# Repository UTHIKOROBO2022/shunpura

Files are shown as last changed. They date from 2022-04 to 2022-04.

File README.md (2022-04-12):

## はじめに  

2021年12月に開催された「第17回全日本学生飛行ロボットコンテスト」に東京大学の有志学生が集まって参加したチーム「瞬着とプライマーよこせ！」のメンバーが、出場機体に搭載した半自動操縦用の制御回路とソースコードを全て公開します！  

<br>

## ファイルリスト  

|ファイル名|説明|
|:--|:--|
|Neve.pdf|回路図PDF|
|Neve.sch|EAGLE回路図ファイル|
|Neve.brd|EAGLEボード図ファイル|
|control_Neve.ino|Arduinoソースファイル|
|CAD|機体の設計データ|

回路図ファイルとボード図ファイルは、Fusion360で作成したものをEAGLE形式で出力しています。

<br>

## 制御について  

本チームは自動操縦部門ではなく一般部門に出場しましたが、飛行を安定させ操縦しやすくするため、独自にマイコンや6軸ジャイロセンサを搭載して半自動操縦を実現しています。すなわち、手元の送信機の左スティックで姿勢角の目標値を与え、機体に搭載したマイコンでそれに追従するよう制御を行っています。また、S.BUS信号のCh.5に半自動操縦のON/OFF、Ch.6に投下機構の動作をアサインしています。

<br>

## 主な使用部品  

|部品名|説明|  
|:--|:--|
|Arduino Nano Every|制御マイコン|  
|GY-521|MPU-6050搭載6軸ジャイロセンサ|  
|Futaba R3001SB|受信機|  

マイコンは必ずArduino Nano Everyを使用します。Arduino Nanoでは動作しません。  
基板上に実装する電子部品については、回路図を参照して下さい。

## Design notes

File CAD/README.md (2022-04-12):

# ひころぼ2021瞬プラ設計データ

公開します

## 概要

- solidworks 2020とautoCADで設計
- unit05となっているのは本番に出場した機体が5号機のため

## ファイル構造

- SHUNPURA_unit05.step
  - fusion360など色々なCADソフトで開ける形式
- data_solidworks
  - solidworksで設計した際の元データ
- data_dxf
  - レーザー加工機をつかったときのDXFデータの残骸

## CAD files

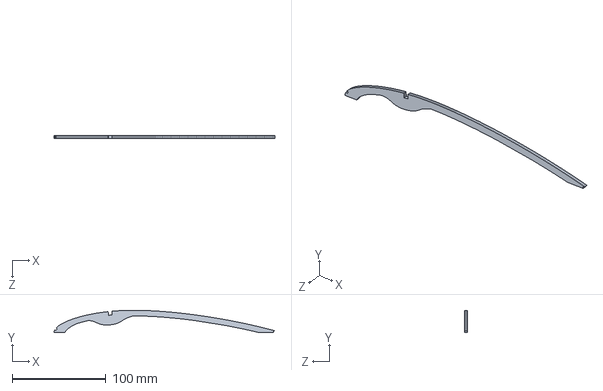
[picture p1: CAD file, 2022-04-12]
CAD/data_solidworks/unit05_mainwing3.SLDPRT
236.3 x 24.0 x 3.00 mm

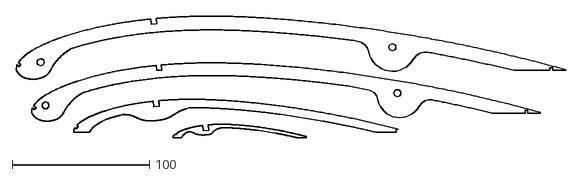
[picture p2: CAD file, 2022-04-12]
CAD/unit05_mainwing.dxf
400.1 x 88.6

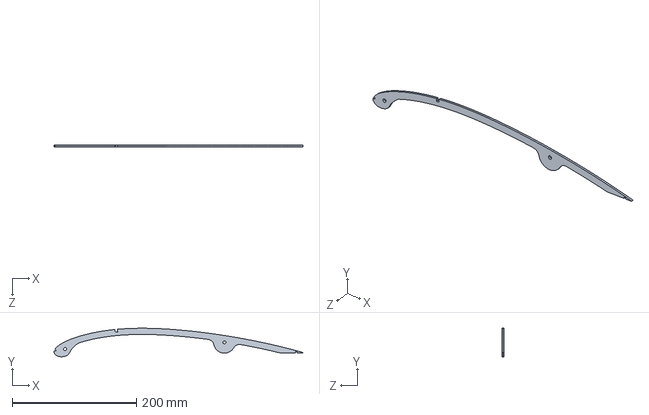
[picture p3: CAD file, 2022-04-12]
CAD/data_solidworks/unit05_mainwing1.SLDPRT
400.1 x 45.9 x 3.00 mm

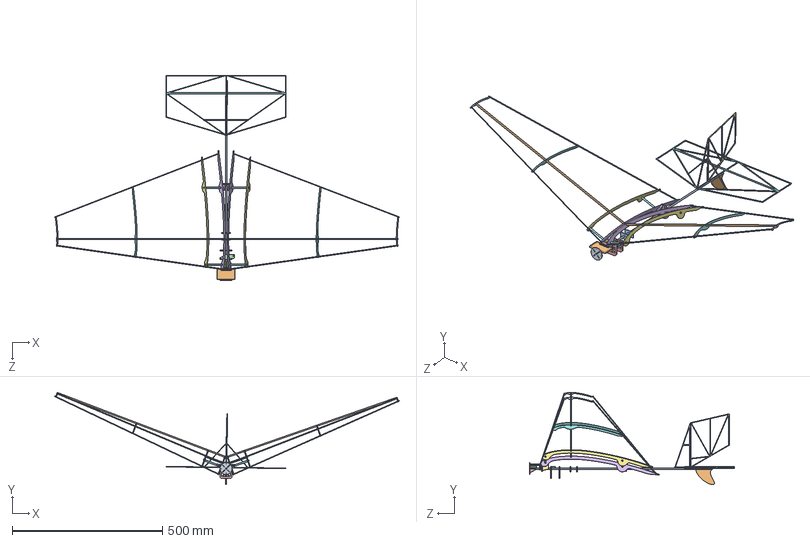
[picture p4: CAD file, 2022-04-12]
CAD/data_solidworks/SHUNPURA_unit05.SLDASM
1148.5 x 307.1 x 683.9 mm
unit05_motormount
unit05_lipoPlate
unit05_rearLipomount x 2
unit05_motormount_support x 2
unit05_motormountsupport x 2
unit05_mainwing1 x 2
unit05_mainwing2 x 2
unit05_mainwing3 x 2
unit05_mainwing4 x 2
unit05_mainspar x 2
unit05_leadingedge x 2
unit05_trailingedge x 2
unit05_mountbase x 2
unit05_pipemountR x 2
unit05_pipemountF x 2
unit05_wingpipe x 4
unit05_body
unit05_rearleg
unit05_servomount x 2
unit05_jyromount
unit05_circuitmount x 2
unit05_ladder1
unit05_ladder2
unit05_elevator

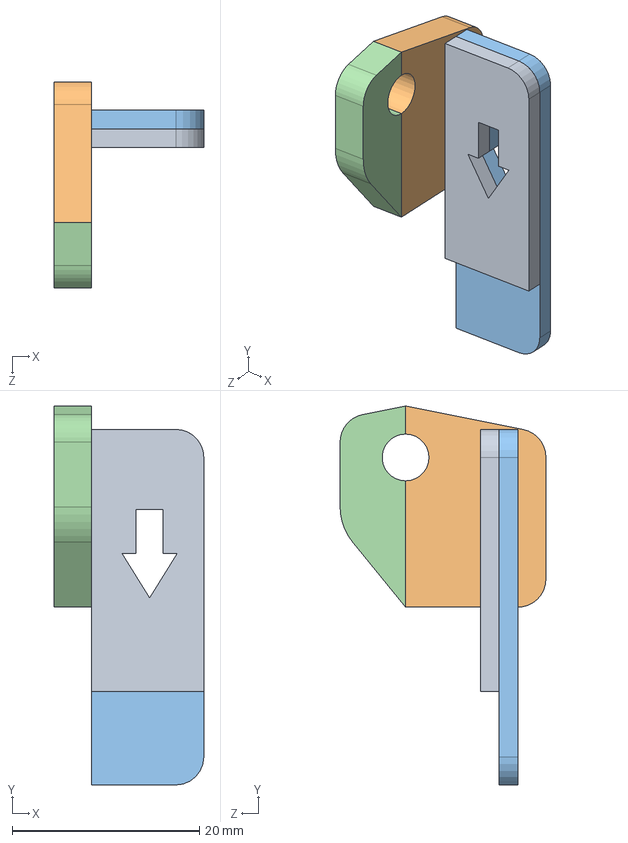
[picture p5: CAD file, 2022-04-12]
CAD/data_solidworks/unit05_ramen_drop.SLDASM
16.0 x 40.5 x 22.0 mm
unit05_drop1
unit05_drop2
unit05_drop3
unit05_drop4

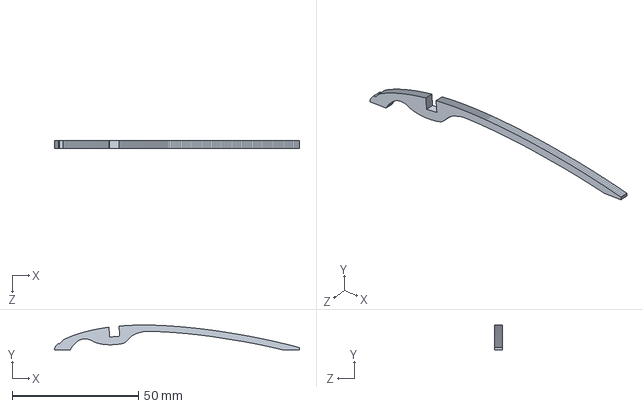
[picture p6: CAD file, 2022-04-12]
CAD/data_solidworks/unit05_mainwing4.SLDPRT
97.1 x 9.88 x 3.00 mm

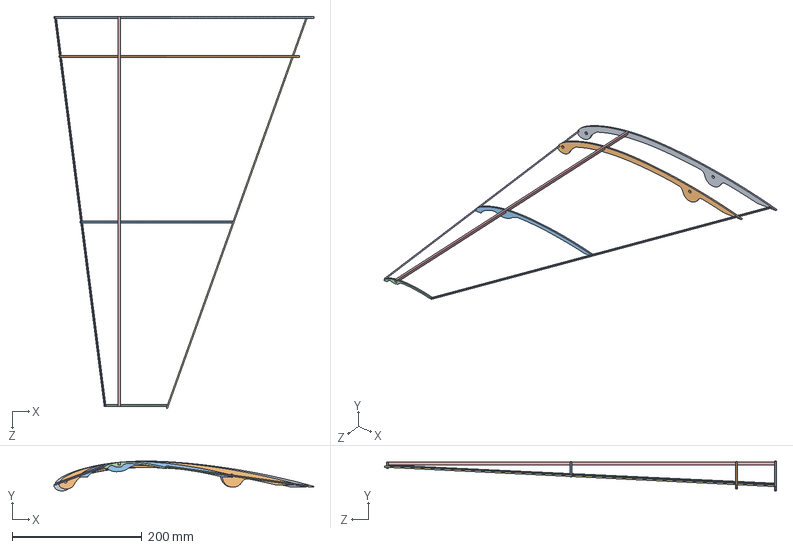
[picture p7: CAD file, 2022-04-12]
CAD/data_solidworks/unit05_mainwingL.SLDASM
400.1 x 45.9 x 603.4 mm
unit05_mainwing1
unit05_mainwing2
unit05_mainwing3
unit05_mainwing4
unit05_mainspar
unit05_leadingedge
unit05_trailingedge

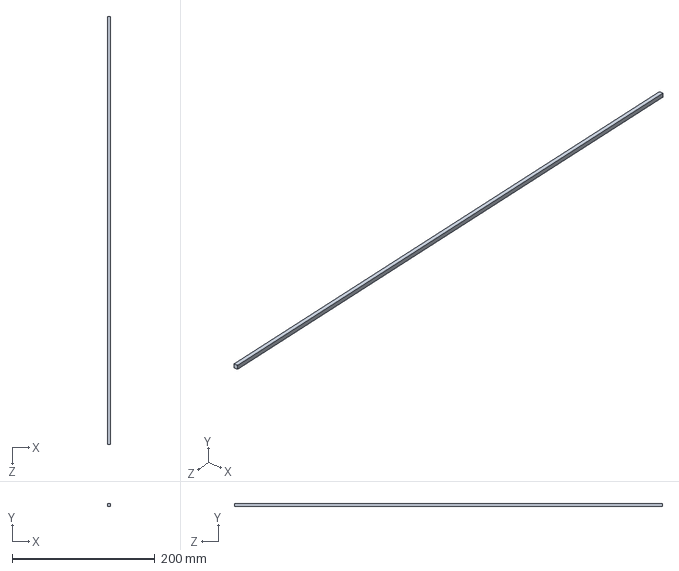
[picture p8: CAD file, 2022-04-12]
CAD/data_solidworks/unit05_mainspar.SLDPRT
4.00 x 4.00 x 600.0 mm

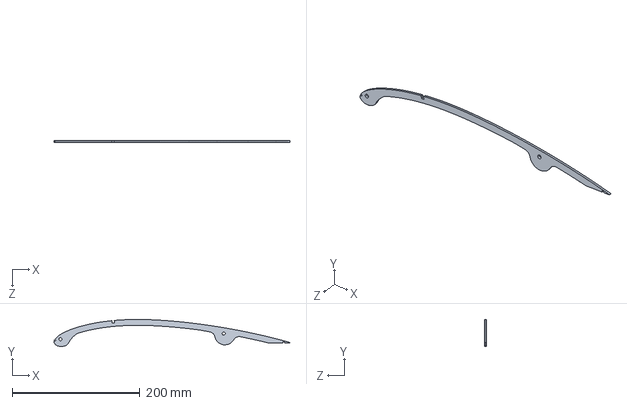
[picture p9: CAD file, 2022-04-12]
CAD/data_solidworks/unit05_mainwing2.SLDPRT
370.1 x 42.5 x 3.00 mm

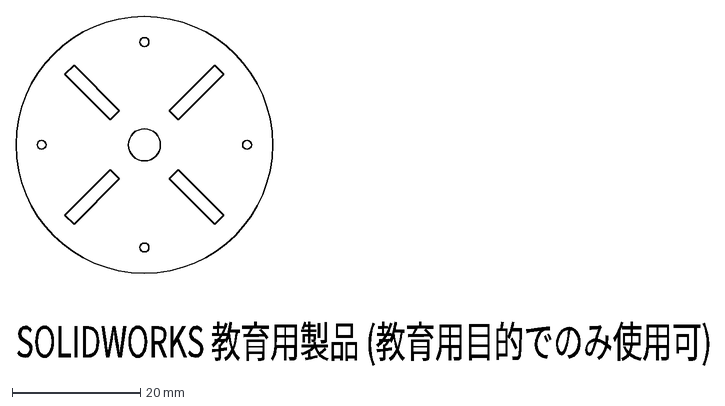
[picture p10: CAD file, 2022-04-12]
CAD/data_dxf/unit05_motormount_veneer.DXF
SOLIDWORKS 教育用製品 (教育用目的でのみ使用可)

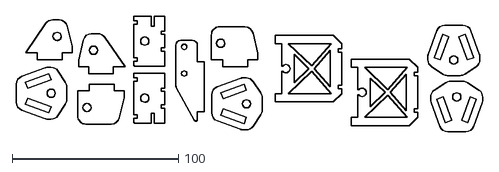
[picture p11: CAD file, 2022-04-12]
CAD/data_dxf/unit05_t4balsa_piover2Rad.dxf
280.9 x 69.6

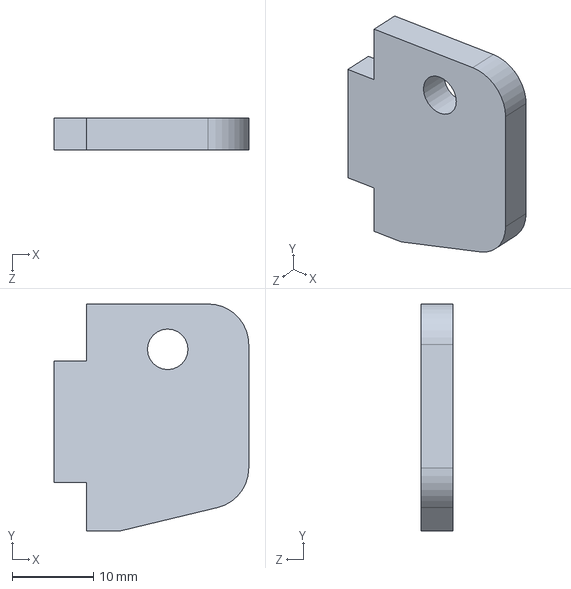
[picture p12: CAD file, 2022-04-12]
CAD/data_solidworks/unit05_GekikomoGearMount.SLDPRT
24.0 x 28.0 x 4.00 mm

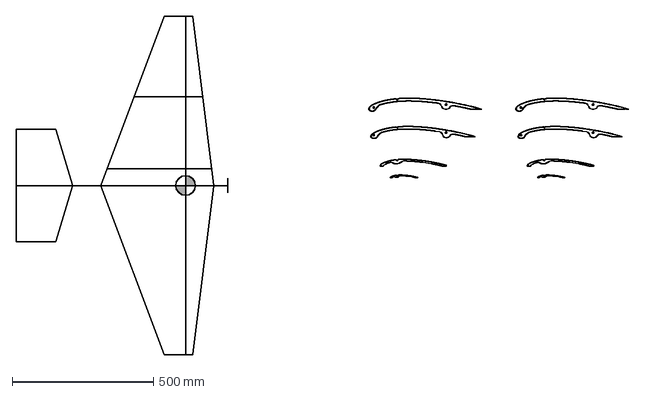
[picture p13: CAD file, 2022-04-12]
CAD/unit05.dxf
2170.0 x 1200.0 mm

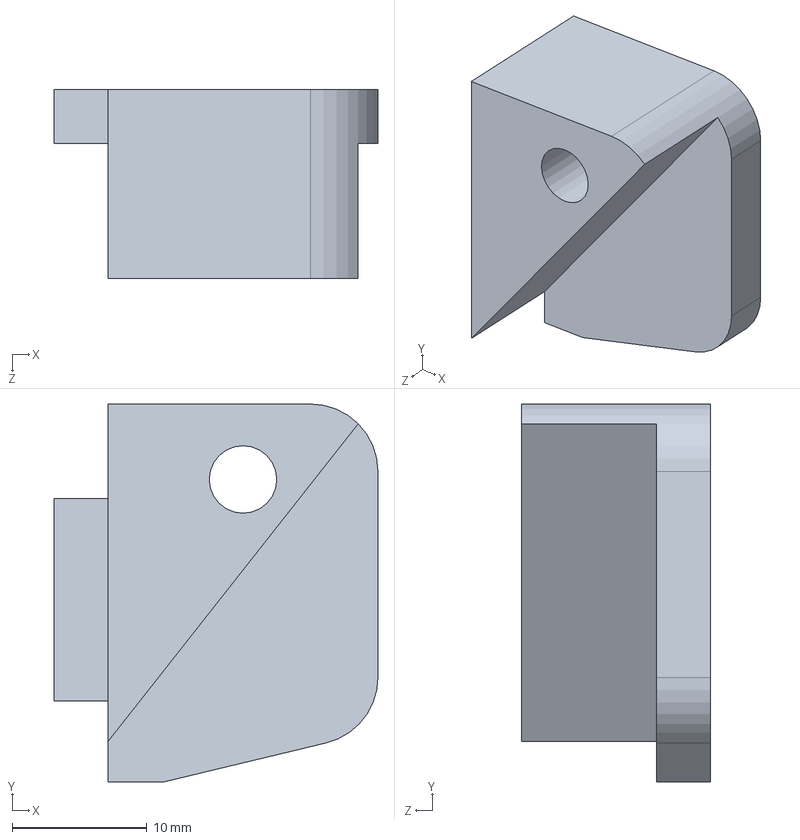
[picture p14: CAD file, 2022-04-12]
CAD/data_dxf/unit05_GekikomoGearMountFront.SLDPRT
24.0 x 28.0 x 14.0 mm

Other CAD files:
CAD/data_solidworks/unit05_mainwingR.SLDASM
CAD/data_solidworks/unit05_drop4.SLDPRT
CAD/data_dxf/unit05_KimoiGears.dxf
CAD/data_solidworks/unit05_takehigogear.SLDPRT
CAD/data_dxf/1216t2veneer.dxf
CAD/data_dxf/unit05_GekikimoGearMountRear.DXF
CAD/data_dxf/unit05_GekikimoGearMountRear.SLDPRT
CAD/data_dxf/unit05_GekikomoGearMountFront.DXF
CAD/data_dxf/unit05_circuitmount.DXF
CAD/data_dxf/unit05_jyromount.DXF
CAD/data_dxf/unit05_lipoPlate.DXF
CAD/data_dxf/unit05_lipomount.DXF
CAD/data_dxf/unit05_motormount.DXF
CAD/data_dxf/unit05_motormountsupport.DXF
CAD/data_dxf/unit05_motormountsupportVe.DXF
CAD/data_dxf/unit05_mountbase.DXF
CAD/data_dxf/unit05_pipeconnecter.DXF
CAD/data_dxf/unit05_pipemountF.DXF
CAD/data_dxf/unit05_pipemountR.DXF
CAD/data_dxf/unit05_rearLipomount.DXF
CAD/data_dxf/unit05_rearleg.DXF
CAD/data_dxf/unit05_servomount.DXF
CAD/data_dxf/unit05_t2veneeer.dxf
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

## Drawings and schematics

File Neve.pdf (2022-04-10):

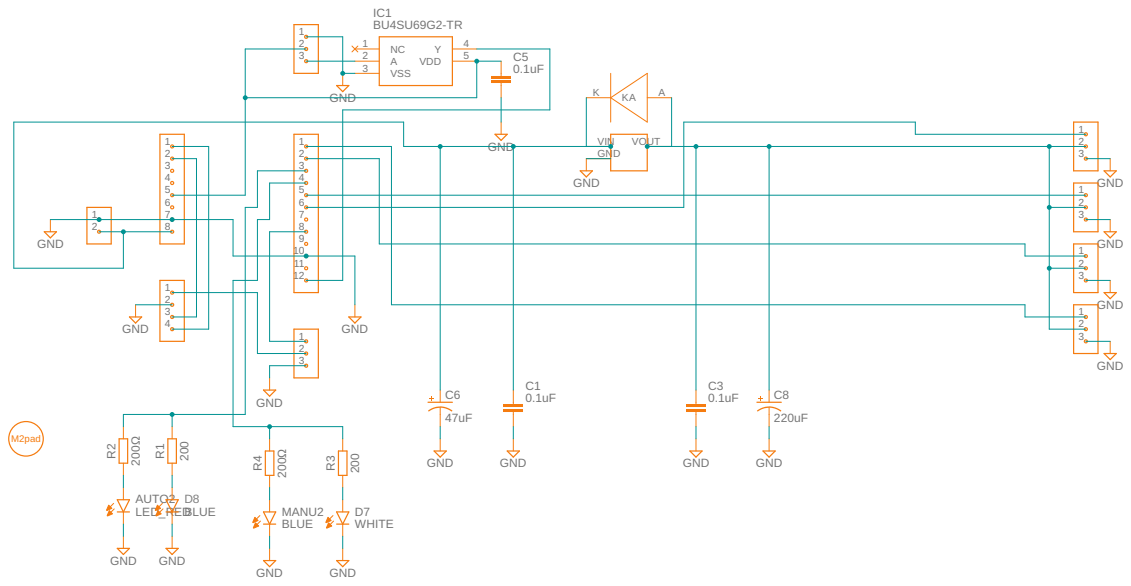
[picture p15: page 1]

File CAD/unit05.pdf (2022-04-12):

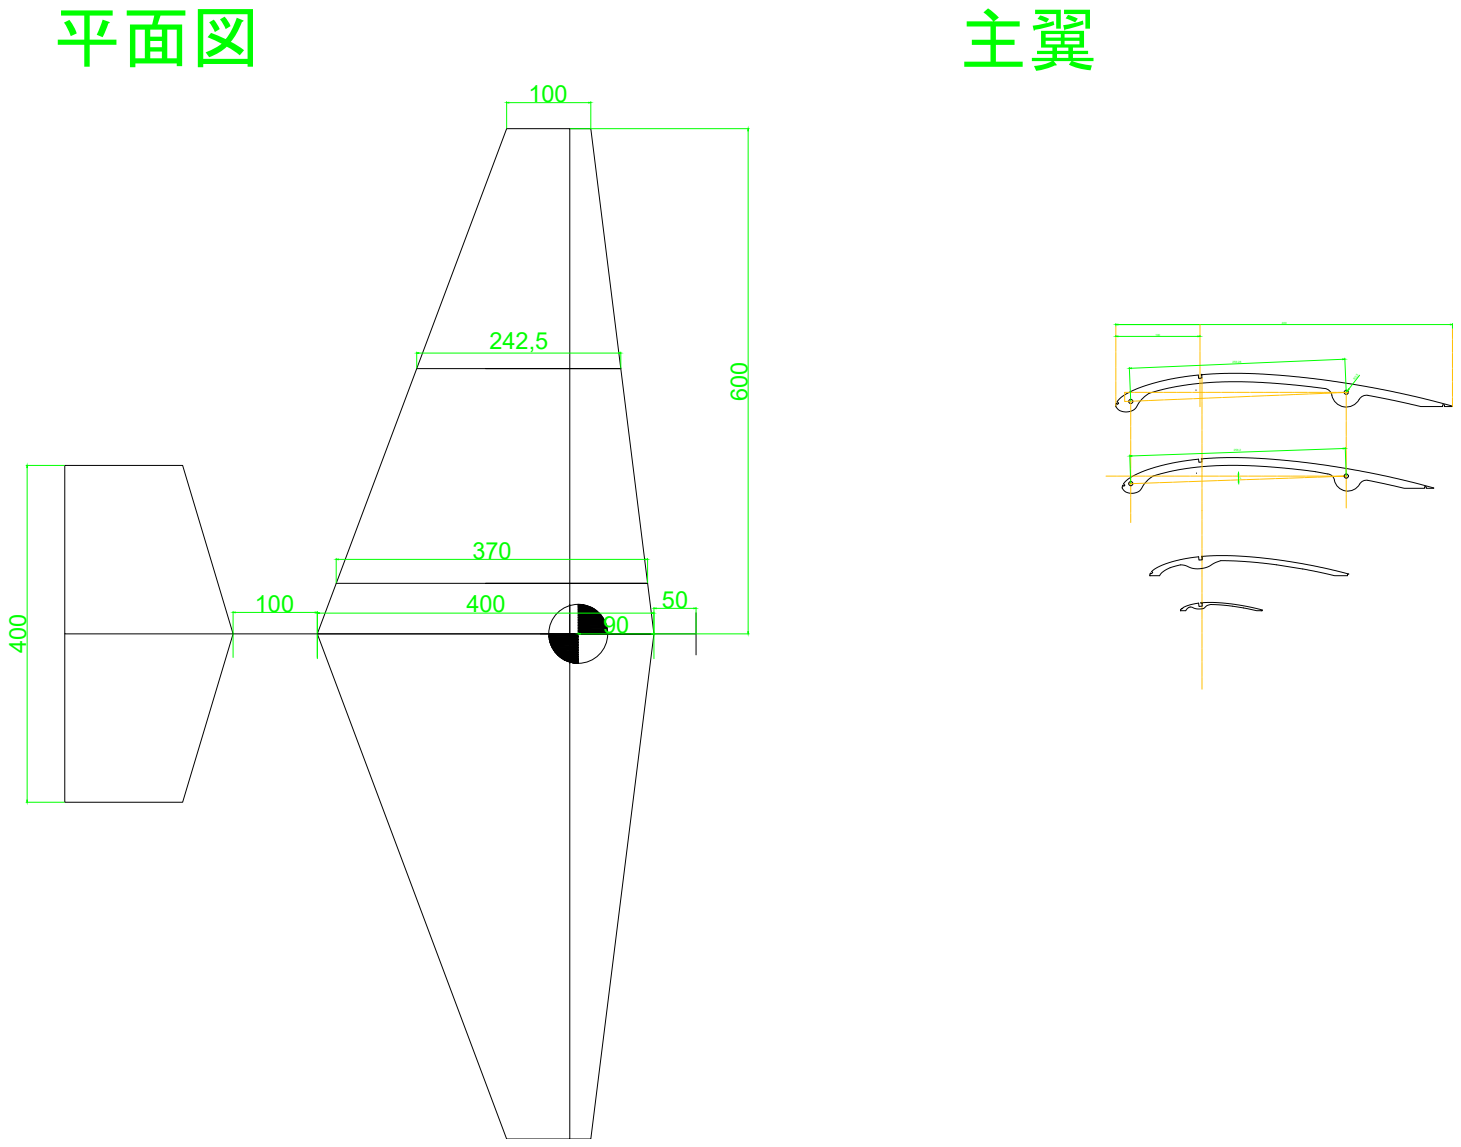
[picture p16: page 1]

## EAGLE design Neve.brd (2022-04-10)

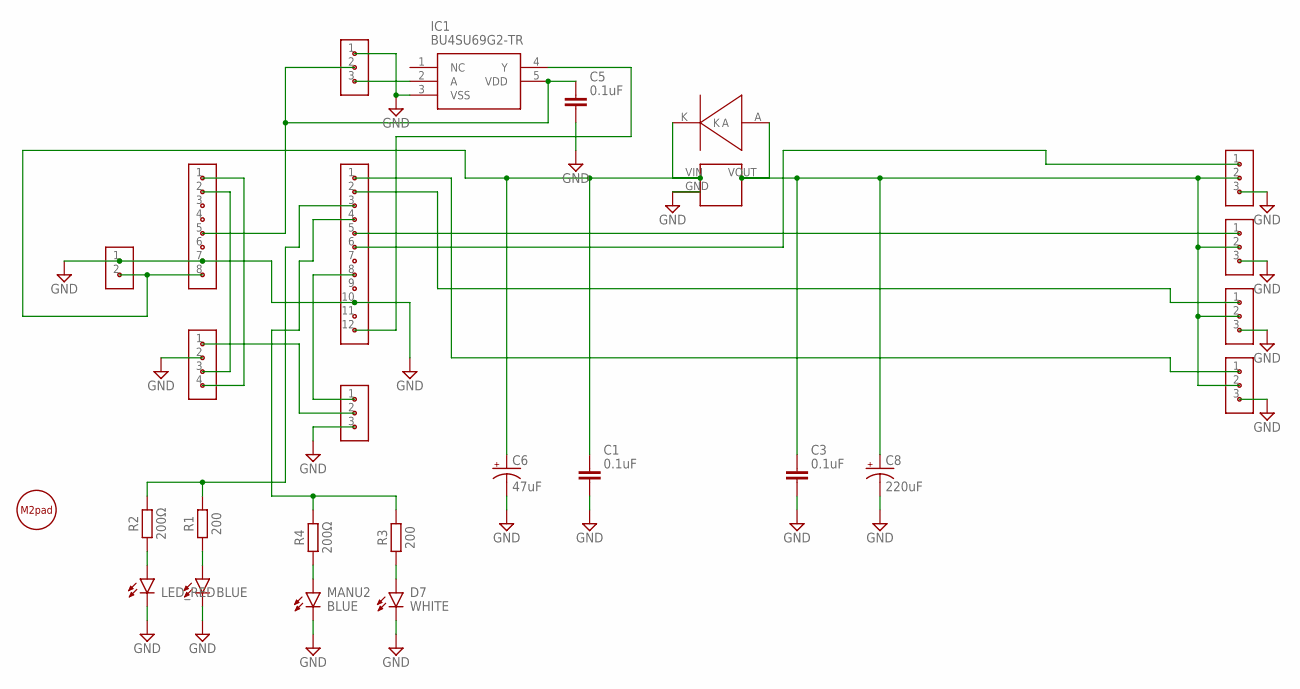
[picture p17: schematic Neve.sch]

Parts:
AUTO2: LED_RED; LEDC1608X65N_RND-R
C1, C3, C5: 0.1uF; CAPC2012X110
C6: 47uF; 153CLV-0605
C8: 220uF; 153CLV-0605
D7: WHITE; LEDC1608X65N_RND-R
D8: BLUE; LEDC1608X65N_RND-R
DIODE1: CRG01
IC1: BU4SU69G2-TR; SOT95P280X125-5N
JP1, JP2, JP3, JP4, JP5, JP8: PIN_1X3
JP6: PIN_1X4
JP7: PIN_1X2
JP9: PIN_1X12
JP10: PIN_1X8
MANU2: BLUE; LEDC1608X65N_RND-R
R1, R3: 200; RESC2012X65
R2, R4: 200Ω; RESC2012X65
RG1: NJM7805SDL1
U$1: M2PAD

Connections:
ARDUINO_5V: C5.1, IC1.5 (VDD), JP8.2, JP10.5
D3_PWM: JP5.1, JP9.8
D5_PWM: JP1.1, JP9.6
D6_PWM: JP2.1, JP9.5
D7_LED_MA: JP9.4, R3.2, R4.2
D8_LED_AU: JP9.3, R1.2, R2.2
D9_PWM: JP3.1, JP9.2
D10_PWM: JP4.1, JP9.1
ESC_5V: JP5.2, JP6.1
GND: AUTO2.C, C1.2, C3.2, C5.2, C6.-, C8.-, D7.C, D8.C, IC1.3 (VSS), JP1.3, JP2.3, JP3.3, JP4.3, JP5.3, JP6.2, JP7.1, JP8.1, JP9.10, JP10.7, MANU2.C, RG1.GND
LIPO_2S: C1.1, C6.+, DIODE1.K, JP7.2, JP10.8, RG1.VIN
unnamed: JP6.3, JP10.2
unnamed: JP6.4, JP10.1
unnamed: MANU2.A, R4.1
unnamed: D8.A, R1.1
unnamed: D7.A, R3.1
unnamed: AUTO2.A, R2.1
SBUS: IC1.2 (A), JP8.3
SERVO_5V: C3.1, C8.+, DIODE1.A, JP1.2, JP2.2, JP3.2, JP4.2, RG1.VOUT
UART: IC1.4 (Y), JP9.12

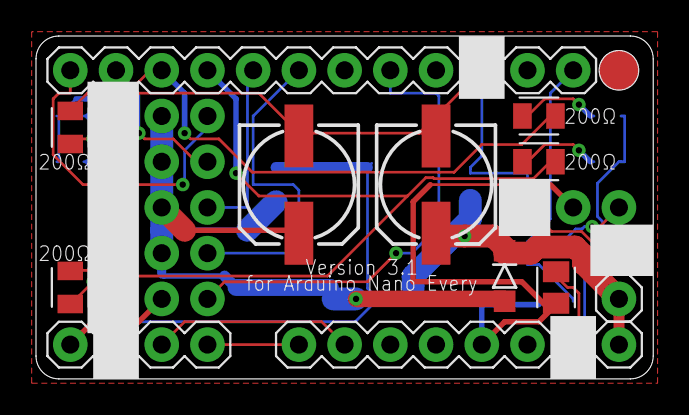
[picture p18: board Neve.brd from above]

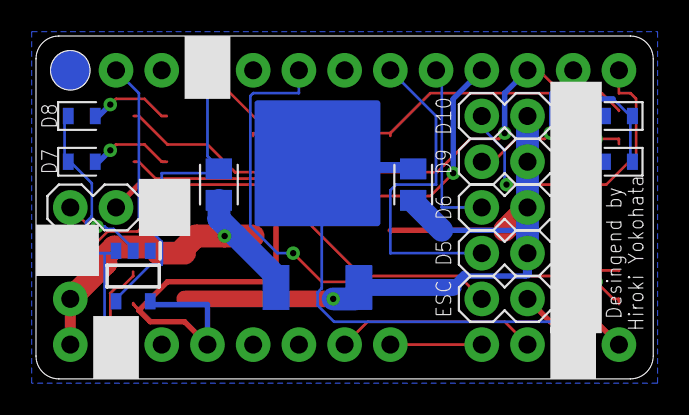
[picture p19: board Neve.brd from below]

Board: 2 copper layers, 34.3 x 19.0 mm, 27 parts (14 on the bottom side), 20 nets.

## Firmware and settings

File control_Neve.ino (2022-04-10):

#include<Servo.h>
#include<I2Cdev.h>
#include<MPU6050_6Axis_MotionApps20.h>
#if I2CDEV_IMPLEMENTATION == I2CDEV_ARDUINO_WIRE
  #include<Wire.h>
#endif

#include "sbus.h"
SbusRx sbus_rx(&Serial1);
SbusTx sbus_tx(&Serial1);

//servo motors and ESC
Servo thr;  
Servo rud;
Servo ele;
//Servo ail;
Servo bomb;

//pins
#define INTERRUPT_PIN (20)
#define LED_MANUAL (7) //WHITE
#define LED_WHITE (7)
#define LED_AUTO (8) //BLUE
#define LED_BLUE (8)
#define THROTTLE_PIN (3)
#define ELEVATOR_PIN (5)
#define RUDDER_PIN (6)
//#define AILERON_PIN (9)
#define BOMB_PIN (10)

//CHANNEL NUMBER
#define CH1 (0)
#define CH2 (1)
#define CH3 (2)
#define CH4 (3)
#define CH5 (4)
#define CH6 (5)
#define CH7 (6)
#define CH8 (7)
#define CH9 (8)
#define CH10 (9)
#define CH11 (10)
#define CH12 (11)
#define CH13 (12)
#define CH14 (13)
#define CH15 (14)
#define CH16 (15)

//servo angles
//#define AILERON_NEUTRAL (90)
//#define AILERON_SEMIRANGE (45)
#define ELEVATOR_NEUTRAL (90)
#define ELEVATOR_SEMIRANGE (45)
#define RUDDER_NEUTRAL (90)
#define RUDDER_SEMIRANGE (45)
#define BOMB_STANDBY (180)
#define BOMB_RELEASE (90)

//CH5 auto control threshold (auto control if less than this value)
#define AUTOCONTROL_CH5_THRESHOLD (1000)

//CH6 CHICKEN RAMEN threshold (release if less than this value)
#define BOMB_CH6_THRESHOLD (1000)

//vars for manual control
int thr_temp;
int rud_temp;
int ele_temp;
//int ail_temp;

//vars for throttle controls
#define THROTTLE_INIT (900)
#define THROTTLE_MIN (1120)
#define THROTTLE_MAX (1999)

//vars for Pcontrol
int tau_rol;
int tau_pit;
int target_rol;
int target_pit;

//vars for MPU6050
MPU6050 mpu;
bool dmpReady=false;    // set true if DMP init was successful
uint8_t mpuIntStatus;   // holds actual interrupt status byte from MPU
uint8_t devStatus;      // return status after each device operation (0 = success, !0 = error)
uint16_t packetSize;    // expected DMP packet size (default is 42 bytes)
uint16_t fifoCount;     // count of all bytes currently in FIFO
uint8_t fifoBuffer[64]; // FIFO storage buffer

//vars for orientation
Quaternion q;           // [w, x, y, z]         quaternion container
VectorFloat gravity;    // [x, y, z]            gravity vector
float ypr[3];           // [yaw, pitch, roll]   yaw/pitch/roll container and gravity vector

#define mimax(x,a,b) ((x)<(a)?(a):(b)<(x)?(b):(x))
#define mimax_abs(x,a) ((x)<-(a)?-(a):(a)<(x)?(a):(x))
int ind;                // loop counter for LED blink


// ================================================================
// ===               INTERRUPT DETECTION ROUTINE                ===
// ================================================================
volatile bool mpuInterrupt=false;     // indicates whether MPU interrupt pin has gone high
void dmpDataReady(){mpuInterrupt=true;}


// ================================================================
// ===                      INITIAL SETUP                       ===
// ================================================================
void setup()
{
  IMUsetup();
  
  pinMode(LED_AUTO,OUTPUT);
  pinMode(LED_MANUAL,OUTPUT);
  
  thr.attach(THROTTLE_PIN);
  thr.writeMicroseconds(THROTTLE_INIT);
  ele.attach(ELEVATOR_PIN);
  ele.write(ELEVATOR_NEUTRAL);
  rud.attach(RUDDER_PIN);
  rud.write(RUDDER_NEUTRAL);
  //ail.attach(AILERON_PIN);
  //ail.write(AILERON_NEUTRAL);
  bomb.attach(BOMB_PIN);
  bomb.write(BOMB_STANDBY);

  sbus_rx.Begin();
  sbus_tx.Begin();

  for(int i=0;i<2;i++)
  {
    digitalWrite(LED_MANUAL,HIGH);
    digitalWrite(LED_AUTO,HIGH);
    delay(100);
    digitalWrite(LED_MANUAL,LOW);
    digitalWrite(LED_AUTO,LOW);
    delay(100);
  }
}


// ================================================================
// ===                    MAIN PROGRAM LOOP                     ===
// ================================================================
void loop()
{
  if(sbus_rx.Read())
  {
      //ail_temp=map(sbus_rx.rx_channels()[CH1],368,1680,-AILERON_SEMIRANGE,AILERON_SEMIRANGE);
      ele_temp=map(sbus_rx.rx_channels()[CH2],1680,368,-ELEVATOR_SEMIRANGE,ELEVATOR_SEMIRANGE);
      thr_temp=map(sbus_rx.rx_channels()[CH3],368,1680,THROTTLE_MIN,THROTTLE_MAX);
      rud_temp=map(sbus_rx.rx_channels()[CH4],368,1680,-RUDDER_SEMIRANGE,RUDDER_SEMIRANGE);

      //CH6 CHICKEN RAMEN
      if(sbus_rx.rx_channels()[CH6]<BOMB_CH6_THRESHOLD)bomb.write(BOMB_RELEASE);
      else bomb.write(BOMB_STANDBY);

      //CH5 auto control
      if(sbus_rx.rx_channels()[CH5]<AUTOCONTROL_CH5_THRESHOLD)
      {
        if(ind<10)digitalWrite(LED_MANUAL,HIGH);
        else digitalWrite(LED_MANUAL,LOW);
        digitalWrite(LED_AUTO,HIGH);
        
        if(!dmpReady)return;
        if(mpu.dmpGetCurrentFIFOPacket(fifoBuffer))
        {
          //update orientation
          mpu.dmpGetQuaternion(&q,fifoBuffer);
          mpu.dmpGetGravity(&gravity,&q);
          mpu.dmpGetYawPitchRoll(ypr,&q,&gravity);

          //elevator (auto control)
          target_pit=ele_temp;
          tau_pit=Pcontrol(ypr[1]*180/M_PI,target_pit,2.0);
          ele.write(mimax_abs(tau_pit,ELEVATOR_SEMIRANGE)+ELEVATOR_NEUTRAL);

          //rudder (auto control)
          target_rol=rud_temp;
          tau_rol=Pcontrol(ypr[2]*180/M_PI,target_rol,1.2);
          rud.write(mimax_abs(tau_rol,RUDDER_SEMIRANGE)+RUDDER_NEUTRAL);

          //aileron (auto control)
          //target_rol=ail_temp;
          //tau_rol=Pcontrol(ypr[2]*180/M_PI,target_rol,0.8);
          //ail.write(mimax_abs(tau_rol,AILERON_SEMIRANGE)+AILERON_NEUTRAL);

          //throttle (manual control)
          thr.writeMicroseconds(thr_temp);
        }
      }
      //manual control
      else
      {
        if(ind<10)digitalWrite(LED_AUTO,HIGH);
        else digitalWrite(LED_AUTO,LOW);
        digitalWrite(LED_MANUAL,HIGH);

        //aileron
        //ail.write(ail_temp+AILERON_NEUTRAL);

        //elevator
        ele.write(ele_temp+ELEVATOR_NEUTRAL);

        //throttle
        thr.writeMicroseconds(thr_temp);

        //rudder
        rud.write(rud_temp+RUDDER_NEUTRAL);
      }
  }
  else
  {
    //Set the SBUS TX data to the received data
    sbus_tx.tx_channels(sbus_rx.rx_channels());
    //Write the data to the servos
    sbus_tx.Write();
  }
  ind=(ind+1)%200;
}


// ================================================================
// ===                        FUNCTIONS                         ===
// ================================================================
int Pcontrol(float current,int target,float Kp)
{
  return Kp*(target-current);
}

void IMUsetup(){
  // join I2C bus (I2Cdev library doesn't do this automatically)
  #if I2CDEV_IMPLEMENTATION == I2CDEV_ARDUINO_WIRE
      Wire.begin();
      Wire.setClock(400000); // 400kHz I2C clock. Comment this line if having compilation difficulties
  #elif I2CDEV_IMPLEMENTATION == I2CDEV_BUILTIN_FASTWIRE
      Fastwire::setup(400, true);
  #endif

  // initialize device
  mpu.initialize();
  pinMode(INTERRUPT_PIN, INPUT);

  // load and configure the DMP
  devStatus = mpu.dmpInitialize();

  // supply your own gyro offsets here, scaled for min sensitivity
  mpu.setXGyroOffset(79);
  mpu.setYGyroOffset(39);
  mpu.setZGyroOffset(-68);
  mpu.setXAccelOffset(-5095);
  mpu.setYAccelOffset(-879);
  mpu.setZAccelOffset(6803);
  // make sure it worked (returns 0 if so)
  if (devStatus == 0) {
      // Calibration Time: generate offsets and calibrate our MPU6050
      mpu.CalibrateAccel(6);
      mpu.CalibrateGyro(6);
      mpu.PrintActiveOffsets();
      // turn on the DMP, now that it's ready
      mpu.setDMPEnabled(true);

      // enable Arduino interrupt detection
      attachInterrupt(digitalPinToInterrupt(INTERRUPT_PIN), dmpDataReady, RISING);
      mpuIntStatus = mpu.getIntStatus();

      // set our DMP Ready flag so the main loop() function knows it's okay to use it
      dmpReady = true;

      // get expected DMP packet size for later comparison
      packetSize = mpu.dmpGetFIFOPacketSize();
  }
}
